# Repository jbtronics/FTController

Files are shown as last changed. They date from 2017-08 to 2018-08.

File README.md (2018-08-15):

# FTController

Der FTController ist eine Motorsteuerung hauptsächlich entwickelt für Fischertechnik. Mittels zweier Joysticks lassen sich 4 analoge Motorausgänge, plus ein Digitalausgang steuern.

## Funktionen
* 4 (bipolare) Analoge Motorausgänge, verschiedene Übertragungsfunktionen auswählbar (digital, linear, quadratisch, logarithmisch, etc.)
* 1 (unipolarer) Digitaler Leistungsausgang (schaltbar über rechten Joysticktaster)
* 1 Impulszähleingang, für Frequenz oder Umdrehungszahlmessung (mit einstellbarem Multiplikator und Teilungsverhältnis)
* Eingangsspannung und Ausgangsstrommessung
* Virtuelle Einrastfunktion: Wird während der Bedienung der Joysticks der linke Joystick doppelt gedrückt, so wird der aktuelle Wert eingefroren (d.h. der Motorwert wird beibehalten auch wenn der Stick losgelassen wird)
* Ansteuermöglichkeit für Raupenketten (Vor/Rück, Links/Rechts-Bewegung an den Joysticks wird auf Raupenkettenantrieb umgesetzt)
* Möglichkeit zur Funkübertragung vorgesehen, d.h. zukünftig auch drahtlose Steuerung möglich.

## Technische Daten
* Eingangsspannungsbereich: 7 - 15 V; Empfohlen: 8 - 10V
* Strombelastbarkeit (Summe aller Ausgänge): max 1,5A
* Strombelastbarkeit *OUT*-Ausgang: max. 500mA
* ATMega328 als Steuerung, d.h. Firmware-Updates via ISP möglich
* Software Arduino kompatibel

## Lizenzen
Für Details siehe `LICENSE.md` in den entsprechenden Verzeichnissen.
* Software: Die Software steht unter der General Public License 3.0
* Hardware: Die Design-Files für die Hardware stehen unter "Creative Commons Attribution-NonCommercial 4.0 International (CC BY-NC 4.0)"

## Benötigte Bauteile
[Hier](https://hackaday.io/project/20349/components) kann eine Liste benötigter Bauteile gefunden werden. Keine Garantie auf Vollständigkeit, sicherer ist der Schaltplan oder die interaktive Bauteileliste die unter `hardware/bom` gefunden werden kann.

## Galerie:
### PCB:
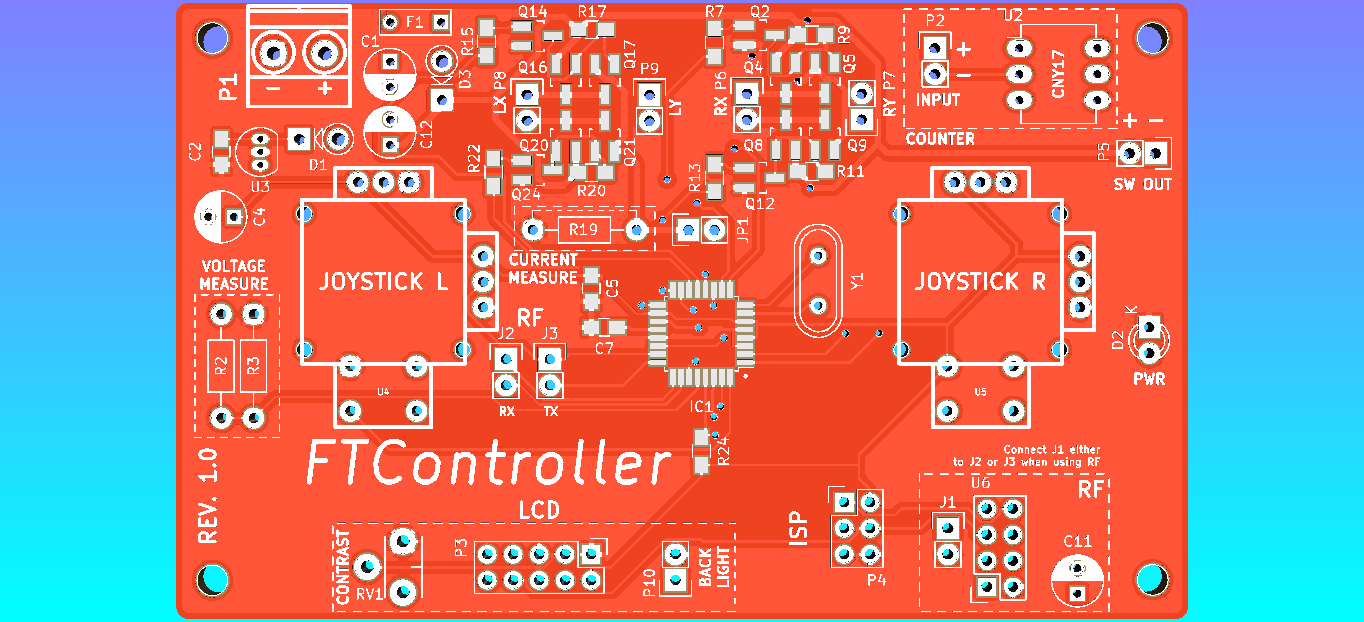
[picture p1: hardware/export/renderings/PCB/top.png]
PCB1

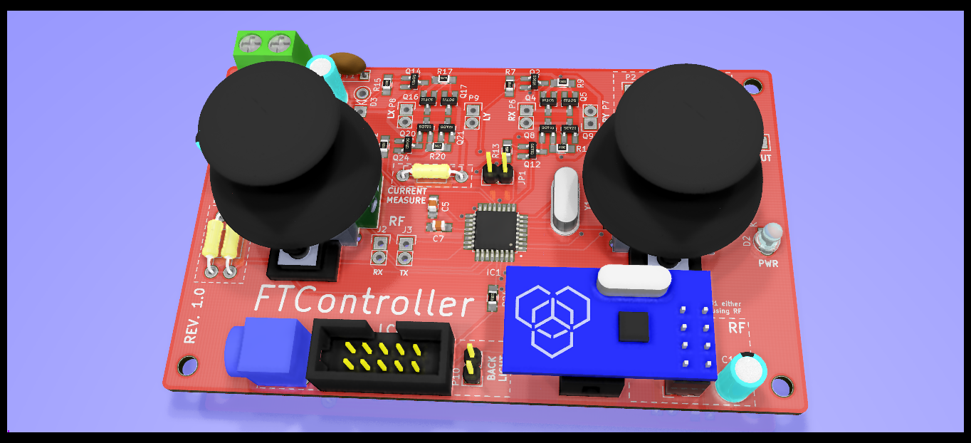
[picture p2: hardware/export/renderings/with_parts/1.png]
PCB2


### Fertiges Gerät:
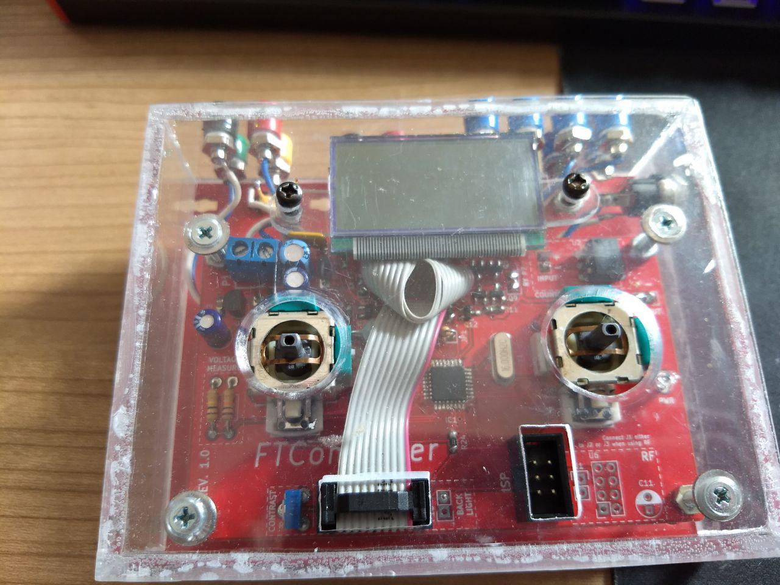
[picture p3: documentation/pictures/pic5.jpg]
finished1

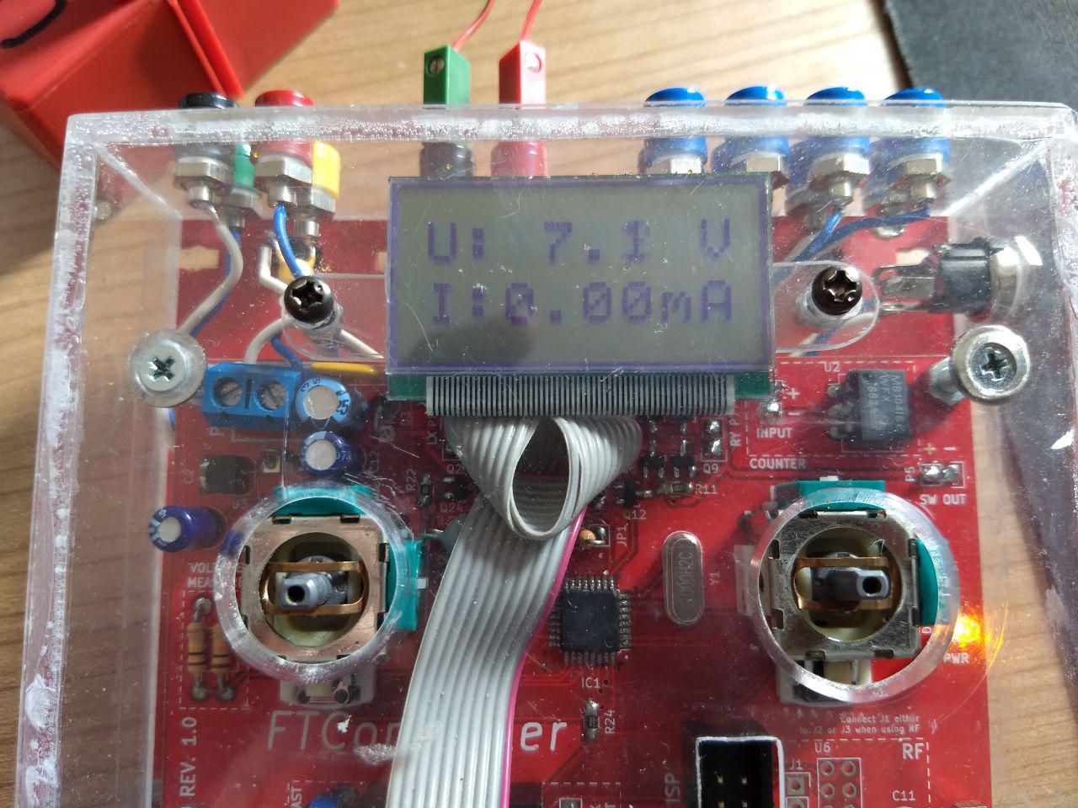
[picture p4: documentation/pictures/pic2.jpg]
finished2


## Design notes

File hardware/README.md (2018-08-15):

# FTController - Hardware

In this folder you can find the KiCAD project for the FTController PCB.
Open FTController with KiCAD 5, and enjoy...

## Some interesting folders

* `bom`: An interactive HTML page which shows, which parts are needed for the PCB and where they are placed. (Generated using [this](https://github.com/openscopeproject/InteractiveHtmlBom))
* `export`: Here you can find some renderings of the PCB
* `gerber`: Here you can find the gerber files for the PCB.

## Changelog

* *Version 1.0*: Initial Version
* *Version 1.1*: Fixed the problem that the Basis pin were used on the CNY17 optocoupler instead of the collector.

## License
The hardware design files are licensed under "Creative Commons Attribution-NonCommercial 4.0 International (CC BY-NC 4.0)". See [here](https://creativecommons.org/licenses/by-nc/4.0/) for more infos.

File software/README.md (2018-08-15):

# FTController - Software
In this folder you can find the software for the FTController:
It can be opened with the Arduino IDE or Visual Studio with the VisualMicro Extension.

Use "Arduino Pro Or Pro Mini" Board with ATMega328 CPU and 16MHz as target and it should work fine with the FTController PCB. The FTController does not have an Serial port, so you will need an ISP Programmer (like the USBasp) to flash the Sketch.

Under the `bin/` folder you can find a compiled Hex file for the FTController, which can be flashed directly onto the FTController board.

### Fuses
TODO

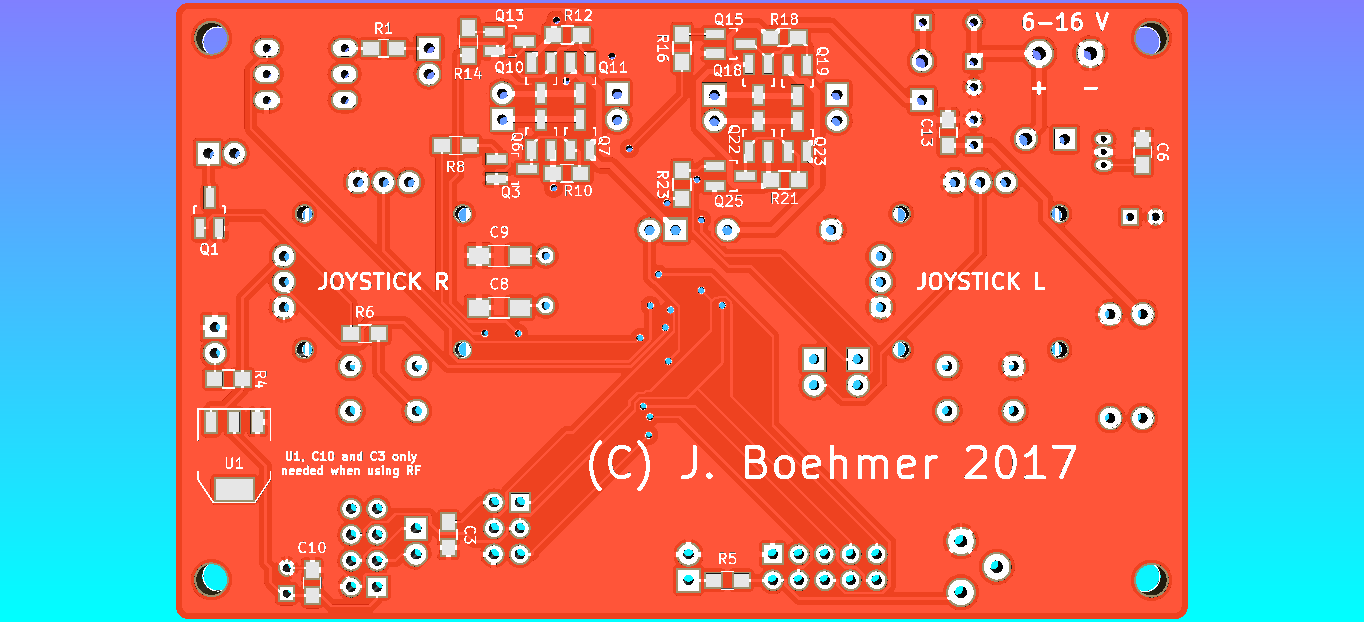
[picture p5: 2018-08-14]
hardware/export/renderings/PCB/bottom.png

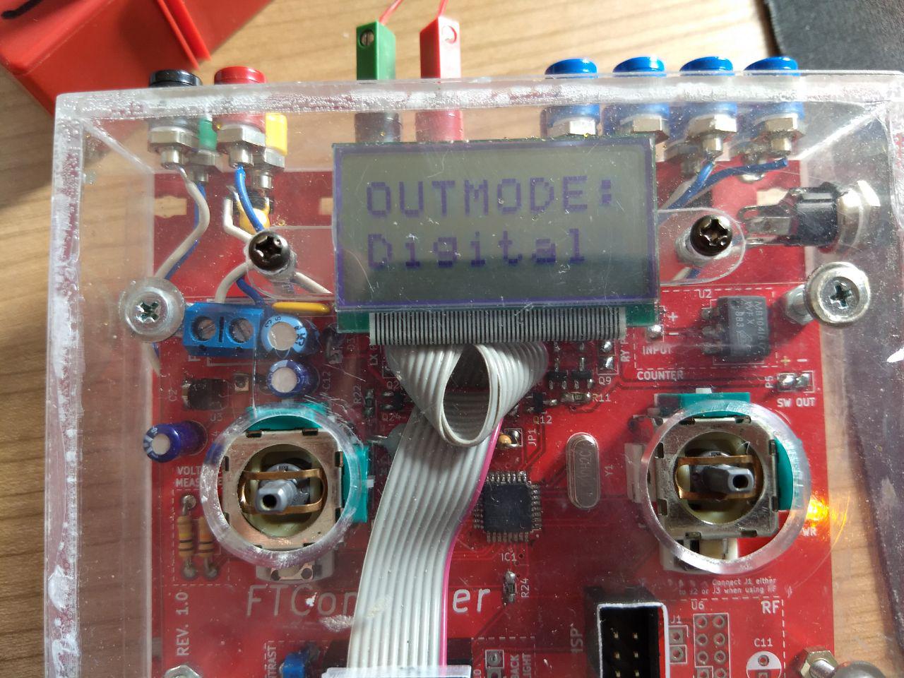
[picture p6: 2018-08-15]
documentation/pictures/pic1.jpg

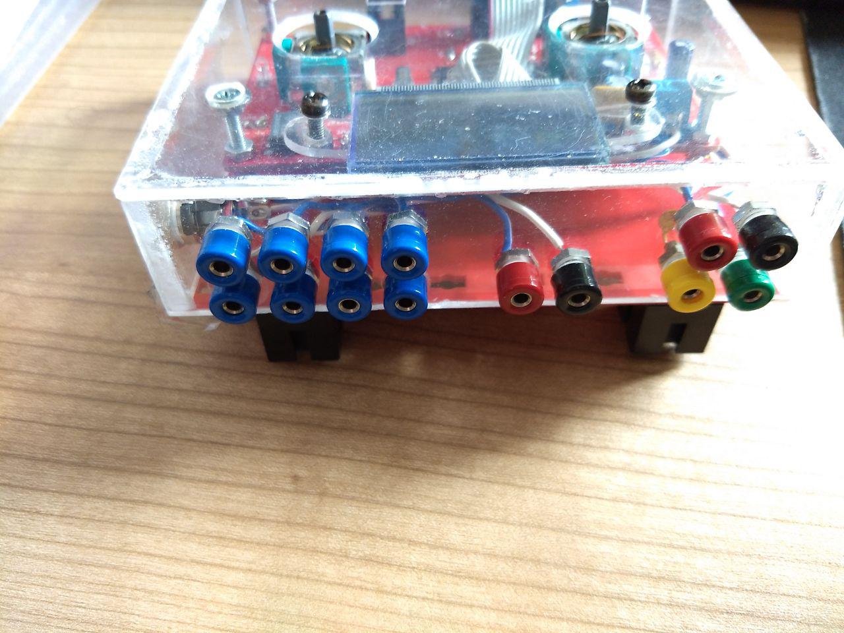
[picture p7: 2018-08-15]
documentation/pictures/pic4.jpg

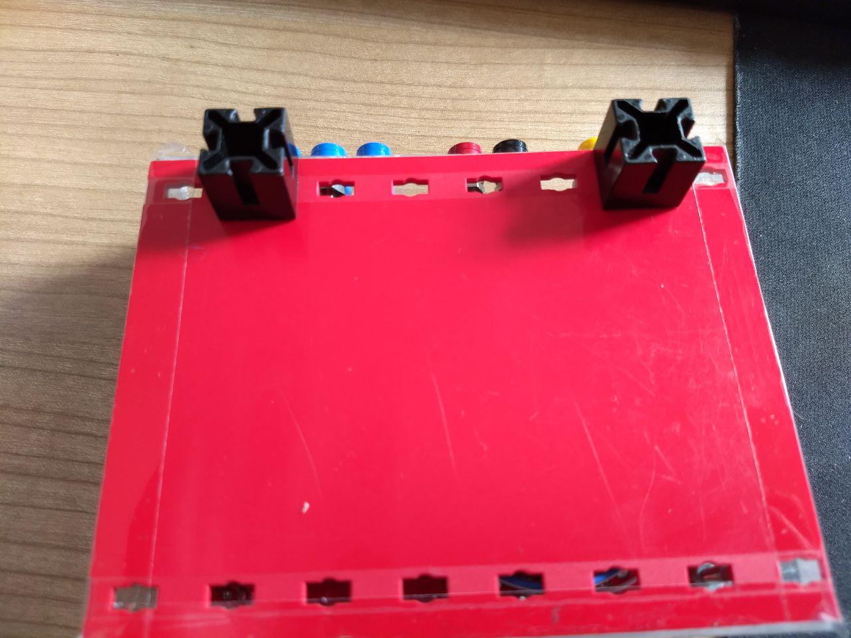
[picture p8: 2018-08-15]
documentation/pictures/pic3.jpg

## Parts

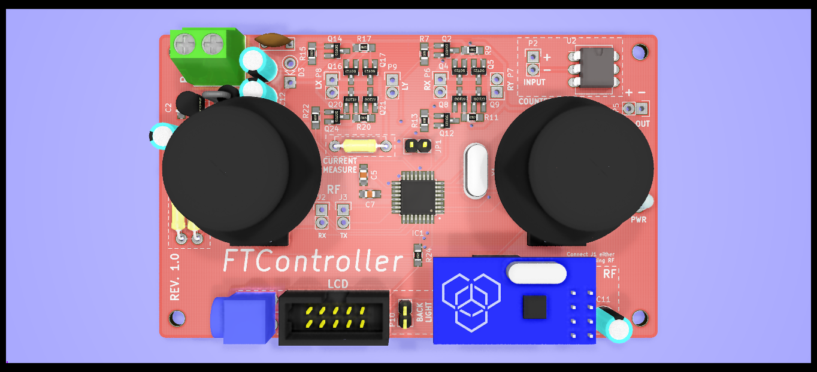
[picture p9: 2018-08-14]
hardware/export/renderings/with_parts/top.png

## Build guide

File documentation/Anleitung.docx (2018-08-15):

# FTController: Handbuch

Firmwareversion: 1.1

# Funktionen

- 4 Analoge Motorausgänge, mit verschiedenen Kennlinien
- 1 Digitaler Motorausgang
- Frequenzzähler / Umdrehungszahlmesser
- Impulszähler
- Spannungs- und Strommessung
- Unterstützung von Multiplikatoren und Teilern für die Zähloperationen
- Notausfunktion.

# Anschlüsse

Der FTController hat verschiede Anschlüsse, deren Aufgaben durch die verwendeten Buchsenfarben unterschieden werden können:

- 1x Stromversorgung, bezeichnet als PWR (rot: +, schwarz: -)
- 4x analoge Ausgänge, steuerbar per Joysticks, bezeichnet als LX, LY, RX und RY (blau)
- 1x digitaler Ausgang, schaltbar mit Drücken des rechten Joysticks, bezeichnet als OUT (rot: +, gelb: -)
- 1x galvanisch getrennter Eingang, bezeichnet als IN (grün: +, schwarz: -). Da der Eingang galvanisch isoliert ist, müssen immer beide Pole des Eingangs verwendet werden. Wenn eine Spannung zwischen den beiden Polen des Eingangs anliegt, so gilt dies als HIGH. Hinweis: Der Eingang detektiert nur steigende Flanken.

# Technische Daten

- Eingangsspannungsbereich: 7V – 15V; Empfohlen: 8 – 10V
- Strombelastbarkeit (Summe aller Ausgänge): max. 1,5A
- Strombelastbarkeit OUT-Ausgang: max. 500Ma

# Inbetriebnahme

1. Legen Sie eine Spannungsquelle (z.B. eine Batterie, Akku, oder Netzteil), ein Stromkabel und den FTController bereit.
2. Verbinden sie den Pluspol der Spannungsquelle (siehe Schritt 1) mit dem Pluspol (rot) des FTControllers unter zu Hilfenahme des Stromkabels, verfahren Sie so ebenfalls mit dem Minuspol der Batterie bzw. des FTControllers.
3. Sollten Sie eine Spannungsquelle verwenden, deren Spannungsausgabe abschaltbar ist, dann versichern Sie sich jetzt, dass die Spannung aktiviert ist. Falls dies nicht der Fall sein, aktivieren Sie die Ausgabe ihre Spannungsquelle. Sollten Sie hierbei Hilfe benötigen, konsultieren Sie bitte das Handbuch ihrer Spannungsquelle.
4. Wenn die Spannung am FTController, sollte die gelbe PWR LED aufleuchten und der FTController sollte starten.
5. Warten Sie die letzte Ausgabe der Startup Sequenz verschwunden ist. Sie können den FTController nun verwenden.

# Bedienung

- Im Steuermodus (nach Start automatisch aktiv), lassen sich mit Hilfe der Joysticks die blauen Analogausgänge steuern: Der linke Joystick steuert mit rechts/links Bewegung den LX Ausgang, mit einer oben/unten Bewegung den LY Ausgang. Der rechte Joystick steuert mit rechts/links den RX Ausgang und mit oben/unten den RY Ausgang
- Mit Druck auf den rechten Joystick, wird auf dem Digitalausgang OUT eine Spannung angelegt.
- Mit einem einfachen Klick des linken Joysticks wird das Menü geöffnet, dieses kann mit einem weiteren Klick auf den linken Joysticks wieder geschlossen werden.
- Mit einem Doppelklick auf den linken Joystick, werden die aktuellen Joystickpositionen eingefroren, d.h. alle Analogausgänge behalten den Wert bei, den sie hatten als die Ausgabe eingefroren wurde, auch wenn die Joysticks losgelassen werden. Das Display des Controllers sollte nun die Ausgabe FREEZED zeigen. Mit einem weiteren Doppelklick auf den linken Joystick wird in den normalen Steuermodus zurückgekehrt.

# Menü:

Das Menü hat drei verschiedene Bereiche zwischen denen mit dem linken Joystick oben/unten gewechselt werden kann: OUTMODE, DISPLAY und CONFIG MENU. Jeder dieser Bereiche hat verschiede Einträge, zwischen denen mit linker Joystick links/rechts gewechselt werden kann. Mit Klick auf den linken Joystick werden die getätigten Einstellungen gespeichert und das Menü geschlossen.

## OUTMODE Menü:

Mit OUTMODE lässt sich festlegen, wie genau die Joystickposition auf die Ausgänge umgesetzt werden soll:

- OUTMODE: None : Wenn dieser Modus gewählt ist, sind die Motorausgänge immer inaktiv, unabhängig von den realen Positionen der Joysticks. Beachten Sie, dass der Digitalausgang, aktivierbar durch Druck auf den rechten Joystick, davon unberührt bleibt.
- OUTMODE: Digital : In diesem Modus sind die Motorausgänge inaktiv, bis ein bestimmter Schwellenwert mit den Joysticks überschritten wird, danach sind die Motorausgänge voll durchgeschaltet.
- OUTMODE: Linear : In diesem Modus wird die Joystickposition linear auf die Ausgänge übertragen, d.h. die Kraft eines angeschlossenen Motors korrespondiert mit der Auslenkung der Joysticks. Beachten Sie, dass dies der Modus mit der höchsten Auflösung (255 Stufen) ist, alle nachfolgenden Analogmodi erlauben nur 26 Stufen.
- OUTMODE: Exp : In diesem Modus wird die Joystickposition mittels einer exponentiellen Kennlinie ausgegeben. Dies erlaubt eine sehr empfindliche Steuerung im niedrigen Bereich der Ausgabewerte.
- OUTMODE: Square : In diesem Modus wird die Joystickposition mittels einer quadratischen Kennlinie ausgegeben. Dies erlaubt eine empfindliche Steuerung im niedrigen Bereich der Ausgabewerte. Dieser Modus ist weniger empfindlich als Exp.
- OUTMODE: Log : In diesem Modus wird die Joystickposition mittels einer logarithmischen Kennlinie ausgegeben. Dies erlaubt eine empfindliche Steuerung im oberen Bereich der Ausgabewerte.
- OUTMODE: Sqrt : In diesem Modus wird die Joystickposition mittels einer Wurzel Kennlinie ausgegeben. Dies erlaubt eine empfindliche Steuerung im oberen Bereich der Ausgabewerte. Dieser Modus ist weniger empfindlich als Log.
- OUTMODE: Tank 2: Dieser Modus erlaubt die analoge Steuerung eines raupenkettengetriebenen Fahrzeuges. Dabei werden die Werte des linken Joysticks mit Hilfe eines Kreuzmischers auf die LX und LY Ausgänge umgesetzt. Das führt dazu das beim Fahren einer Kurve beide Motoren gegensinnig angesteuert werden.

Nur der linke Joystick hat diesen Modus, der rechte Joystick erlaubt die normale lineare Steuerung von Verbrauchern.

- OUTMODE: Tank 1: Dieser Modus erlaubt ähnlich wie Tank 2, die Steuerung eines kettengetriebenen Fahrzeuges, mit dem Unterschied, dass für eine Rechts/Links-Kurve nur ein Motor angesteuert wird.

## DISPLAY Menü:

Mit DISPLAY lässt sich festlegen, was für eine Anzeige während des Steuermodus erfolgen soll, so kann z.B. die aktuelle Spannung oder der Stromfluss angezeigt werden:

- DISPLAY: In Vals. : In diesem Modus werden die gemessenen Joystickpositionen ausgegeben. Diese liegen im Bereich zwischen -512 und 512, wobei ein Wert nahe 0 den Ruhezustand angibt.
- DISPLAY: Voltages. : In diesem Modus werden die Spannungen des FTControllers gemessen und ausgegeben. Die IN: Zeile gibt die Eingangsspannung an, während die 5V: Zeile die Spannung des Prozessors angibt (sieh sollte immer um ca. 5V liegen).
- DISPLAY: Power : In diesem Modus wird die Eingangsspannung in der Zeile U: dargestellt, während der Strom, der durch die Ausgänge fließt in der Zeile I: dargestellt wird. Beachten Sie, dass der Strom einige Sekunden zur Aktualisierung benötigt. Weiterhin fließen in die Strommessung nur die Ströme der Analogausgänge und nicht der Strom des Digitalausgang ein.
- DISPLAY: Out Vals. : In diesem Modus werden die Stärke der Ausgaben für jeden Analogausgang dargestellt. Diese reichen von -255 bis 255, wobei 0 keine Ausgabe bedeutet. Beachten sie, dass dieser Modus nicht bei den OUTMODEs LINEAR oder DIGITAL funktioniert.
- DISPLAY: RPM : In diesem Modus wird die Frequenz bzw. daraus abgeleitet, die Umdrehungszahl die am Eingang anliegt gemessen. Die erste Zeile der Ausgabe, gibt die Einheit an mit der die Ausgabe erfolgt, während die zweite Zeile den gemessenen Wert zeigt. Sollte die Input Entprellung (siehe I.DEBNC. im Config menu) aktiviert sein, so wird dies mit einem D in der ersten Zeile kenntlich gemacht. Ein möglicherweiser aktiver Multiplikator (siehe C.MULTI und C.DIVIDE) wird mit x gekennzeichnet. Die Einheit mit der die Ausgabe erfolgt kann mit der C.UNIT Einstellung im Config menu verändert werden. Die maximale Frequenz, die gemessen werden kann, beträgt ca. 100kHz.
- DISPLAY: COUNTER : In diesem Modus wird für jede aufsteigende Flanke am Eingang der Zähler inkrementiert. Dabei werden die Multiplikatoren und Divisor Einstellungen berücksichtigt. Um den Zähler auf 0 zurücksetzen, muss man einen Doppelklick auf den linken Joystick durchführen.
- DISPLAY: TEMP : Dieser Modus zeigt die ungefähre Temperatur des Prozessors in Grad Celsius an. Da der Temperatursensor nicht kalibriert ist, sollte nur die Veränderungen des Temperaturwertes zur Kontrolle herangezogen werden, nicht der absolute Wert.

## CONFIG MENU Menü

In diesem Menü lassen sich verschieden Einstellungen treffen, die vor allem den COUNTER/RPM Modus betreffen. Mit dem linken Joystick links/rechts lässt sich die Einstellung auswählen, die bearbeitet werden soll und mit dem rechten Stick lässt sich der Wert verändern. Soll eine Zahl eingegeben werden, so verändert rechter Stick rechts/links den Wert in 1er-Schritten, während oben/unten den Wert in 10er-Schritten verändert:

- EM. HALT: Nothalt-Funktion: Wenn diese Funktion aktiviert ist, dann werden, sobald eine postive Flanke am Eingang erkannt wird, alle Ausgänge deaktiviert. Auf dem Display sollte dann die Ausgabe Em.Halt! PressBTN erscheinen. Wenn man wieder in den normalen Modus zurückkehren will, so muss man den linken Joystick drücken.
- C. UNIT: Mit dieser Einstellung lässt sich die Einheit einstellen, mit der im RPM Modus die Ausgabe erfolgen soll. Mögliche Werte: RPM oder Hz.
- I. DEBNC.: Entprellung. Wenn diese Einstellung aktiv ist, dann wird der Eingang entprellt, d.h. die Anzahl der maximalen Flanken pro Sekunde wird reduziert. Diese Einstellung sollte aktiviert werden, wenn bei einem einzigen Schalterklick, mehrere Klicks gezählt werden.
- C. MULTI: Dieser Wert stellt den Multiplikator ein, mit dem die Zahl der Inputsignale multipliziert wird. Steht C.MULTI z.B. auf 2, so zählt jedes Eingangssignal doppelt.
- C. DIVIDE: Dieser Wert stellt den Multiplikator ein, mit dem die Zahl der Inputsignale dividiert wird. Steht C.DIVIDE z.B. auf 2, so muss zwei Mal ein Signal auftreten, damit der Wert hochgezählt wird.

# Weitere Hinweise:

- Erscheint beim Start die Meldung RELEASE STICKS!, so müssen die Sticks losgelassen werden, um fortzufahren. Dies verhindert, dass ein Motor sofort nach dem Start aktiviert wird.
- Erscheint die Meldung Ov.Curr! PressBTN, so wurde ein zu hoher Strom gemessen. Dies kann eventuell auf einen Kurzschluss hinweisen. Möchte man fortfahren, so muss der linke Joystick gedrückt werden.
- Startet sich der FTController ohne Unterbrechung der Stromversorgung selbständig neu, so weist dies auf einen Kurzschluss hin. Beheben Sie diesen bevor Sie fortfahren.

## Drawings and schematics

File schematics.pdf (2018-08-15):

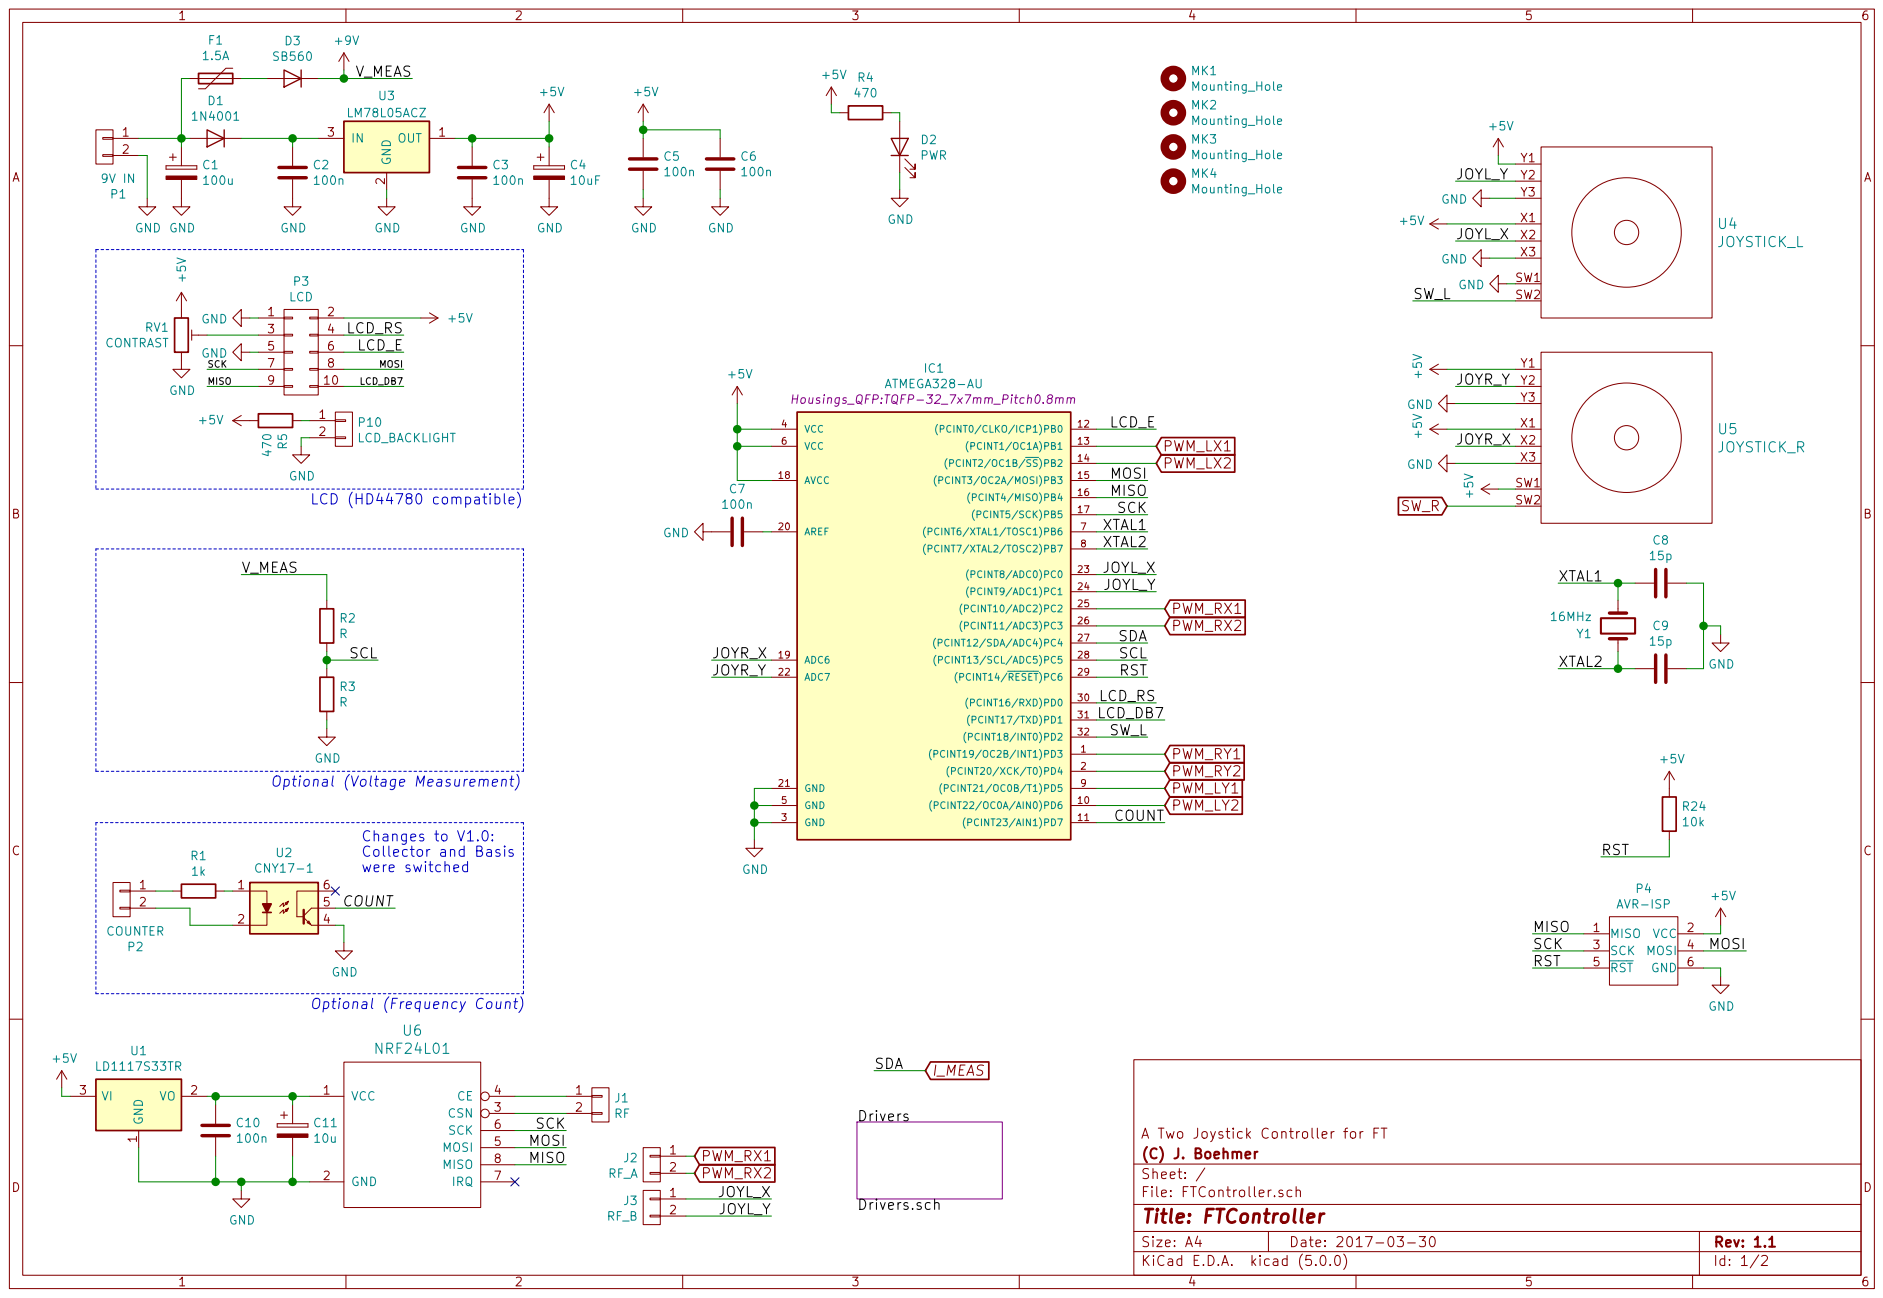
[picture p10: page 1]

Collector and Basis were switched

A Two Joystick Controller for FT
Id: 1/2 Title: FTController File: FTController.sch Sheet: / (C) J. Boehmer

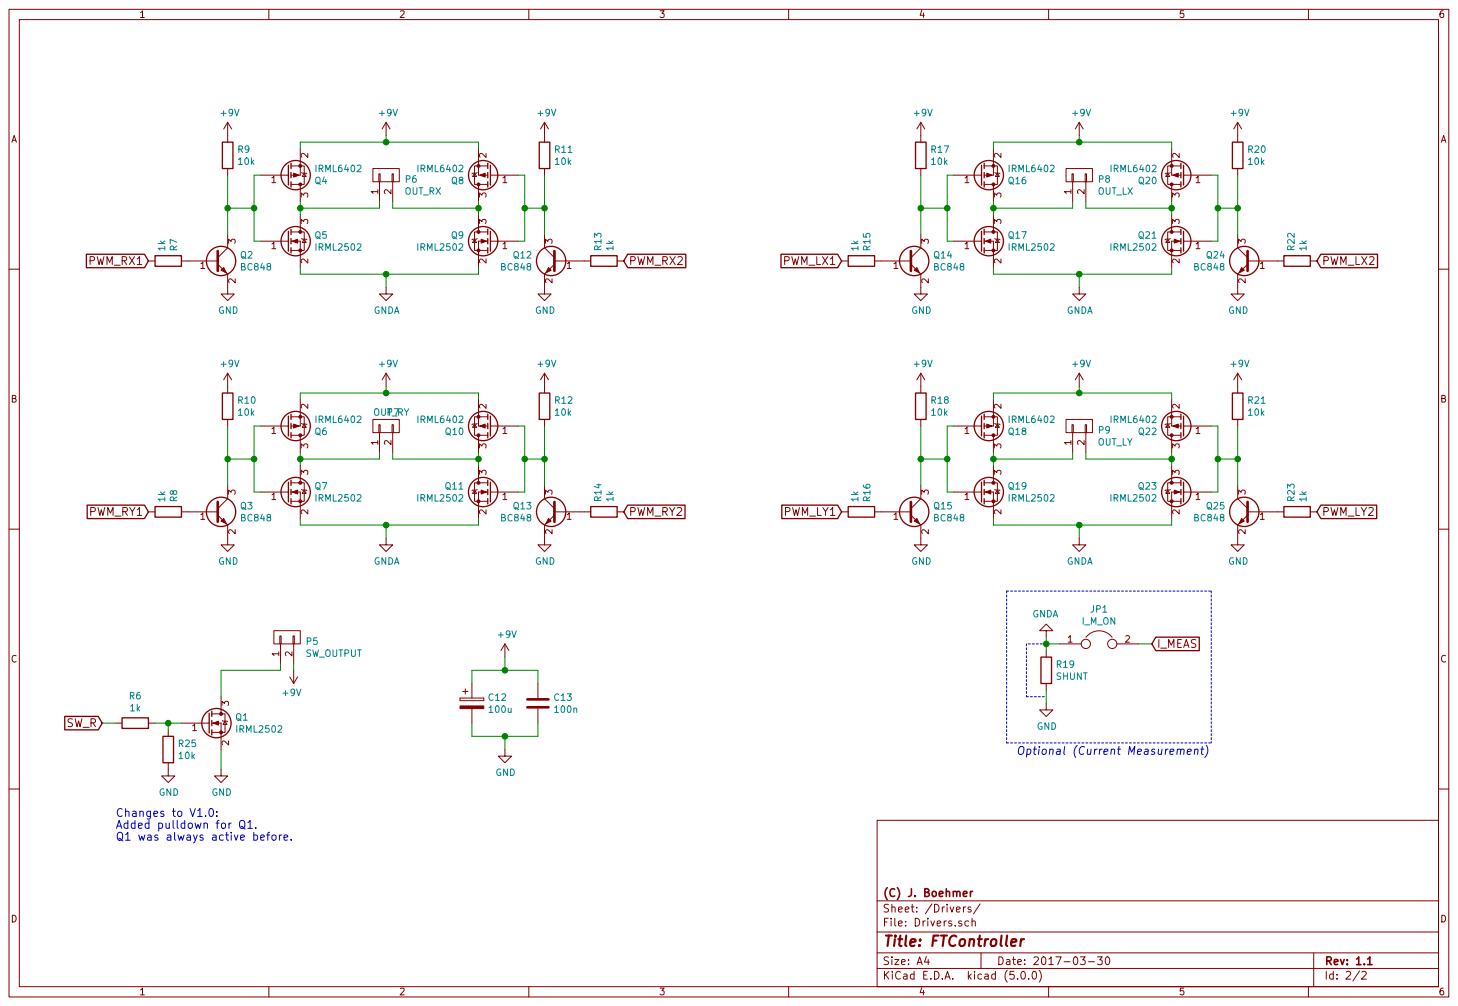
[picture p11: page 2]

Added pulldown for Q1.
Q1 was always active before.

Id: 2/2 Title: FTController File: Drivers.sch Sheet: /Drivers/ (C) J. Boehmer

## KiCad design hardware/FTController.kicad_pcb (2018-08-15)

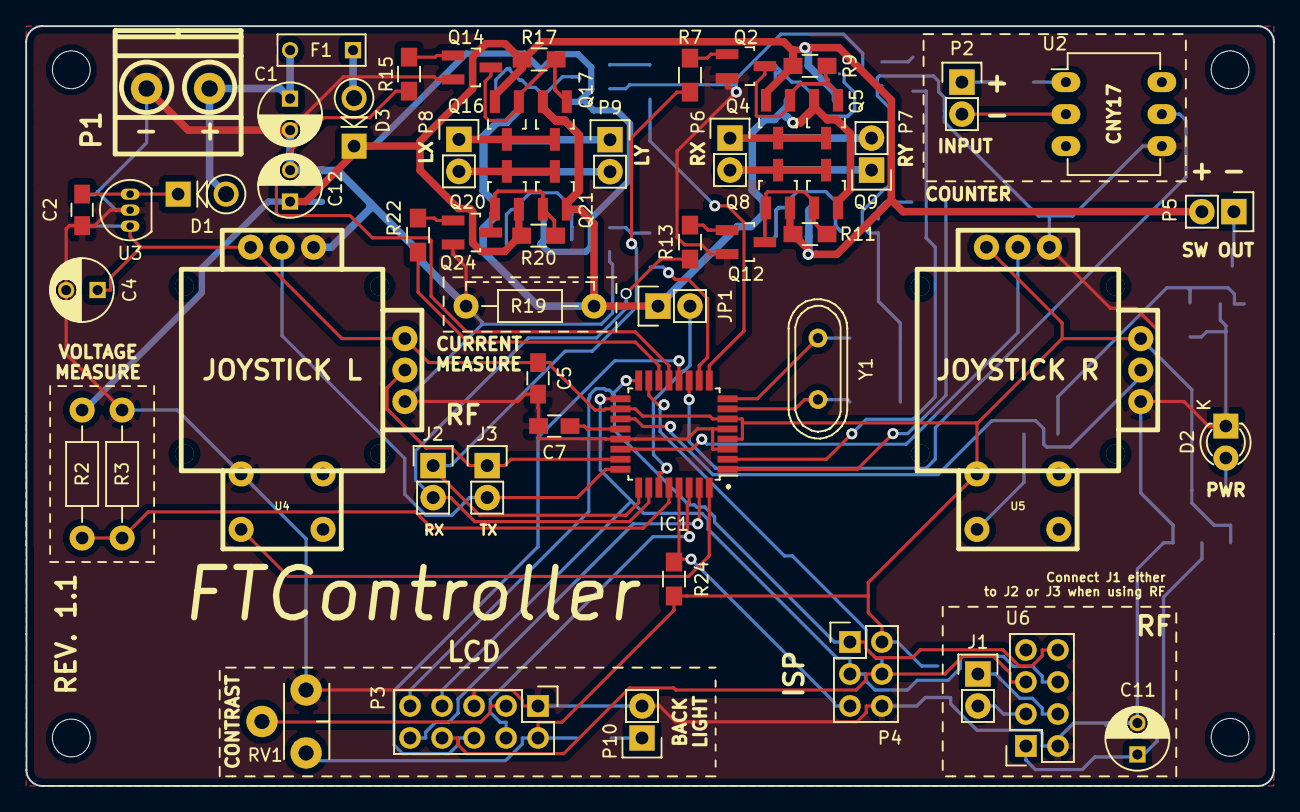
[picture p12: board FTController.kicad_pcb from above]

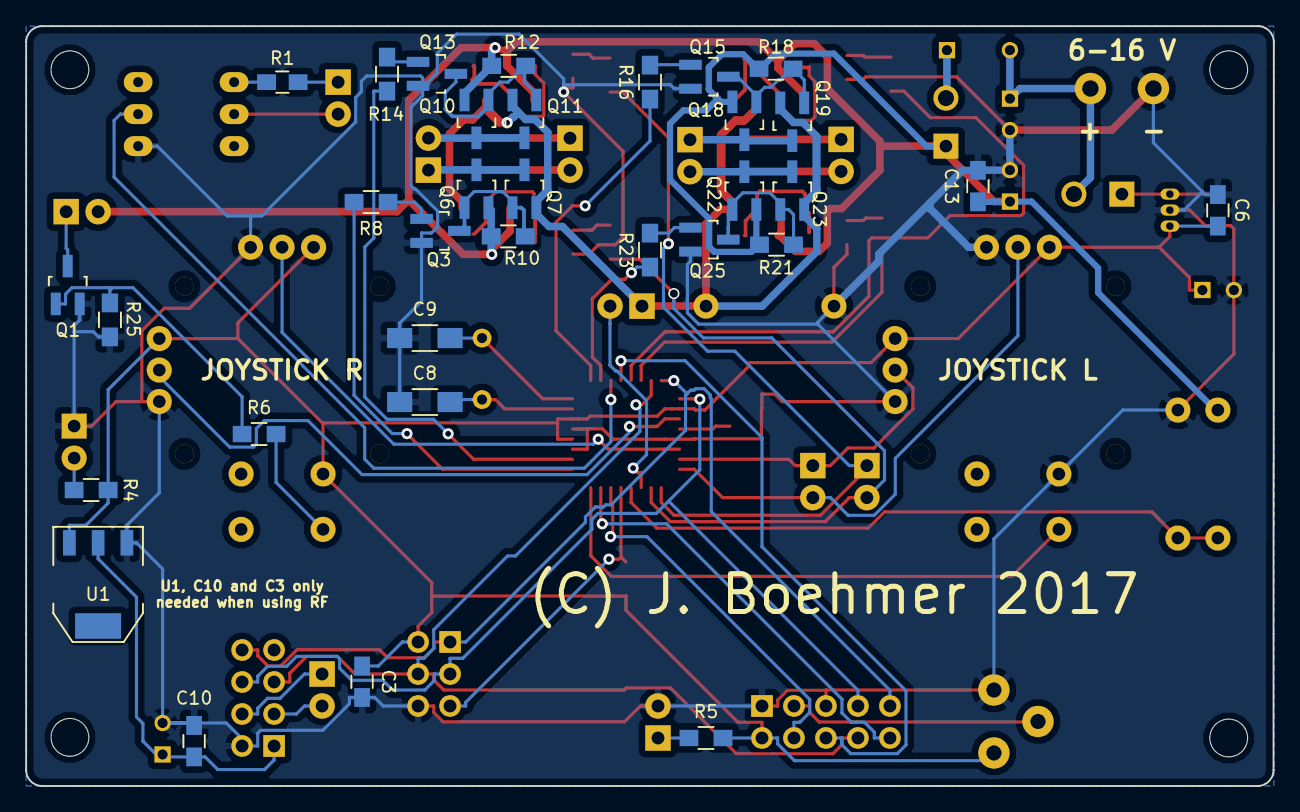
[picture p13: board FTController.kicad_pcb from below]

Board: 2 copper layers, 99.1 x 60.3 mm, 94 parts (33 on the bottom side), 69 nets.

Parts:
C1, C12: 100u; C_Radial_D5_L11_P2.5
C2, C3, C5, C6, C7, C10, C13: 100n; C_0805_HandSoldering
C4: 10uF; C_Radial_D5_L11_P2.5
C8, C9: 15p; C_1206_HandSoldering
C11: 10u; C_Radial_D5_L11_P2.5
D1: 1N4001; Diode_DO-41_SOD81_Vertical_KathodeUp
D2: PWR; LED-3MM
D3: SB560; Diode_DO-41_SOD81_Vertical_KathodeUp
F1: 1.5A; C_Rect_L7_W2.5_P5
IC1: ATMEGA328-AU; TQFP-32_7x7mm_Pitch0.8mm
J1: RF; Pin_Header_Straight_1x02
J2: RF_A; Pin_Header_Straight_1x02
J3: RF_B; Pin_Header_Straight_1x02
JP1: I_M_ON; Pin_Header_Straight_1x02
MK1, MK2, MK3, MK4: Mounting_Hole; MountingHole_3mm
P1: 9V IN; mkds_1,5-2
P2: COUNTER; Pin_Header_Straight_1x02
P3: LCD; Pin_Header_Straight_2x05
P4: AVR-ISP; Pin_Header_Straight_2x03
P5: SW_OUTPUT; Pin_Header_Straight_1x02
P6: OUT_RX; Pin_Header_Straight_1x02
P7: OUT_RY; Pin_Header_Straight_1x02
P8: OUT_LX; Pin_Header_Straight_1x02
P9: OUT_LY; Pin_Header_Straight_1x02
P10: LCD_BACKLIGHT; Pin_Header_Straight_1x02
Q1, Q5, Q7, Q9, Q11, Q17, Q19, Q21, Q23: IRML2502; SOT-23_Handsoldering
Q2, Q3, Q12, Q13, Q14, Q15, Q24, Q25: BC848; SOT-23_Handsoldering
Q4, Q6, Q8, Q10, Q16, Q18, Q20, Q22: IRML6402; SOT-23_Handsoldering
R1: 1k; C_0805_HandSoldering
R2, R3: R; Resistor_Horizontal_RM10mm
R4, R5: 470; R_0805_HandSoldering
R6, R7, R8, R13, R14, R15, R16, R22, R23: 1k; R_0805_HandSoldering
R9, R10, R11, R12, R17, R18, R20, R21, R24, R25: 10k; R_0805_HandSoldering
R19: SHUNT; Resistor_Horizontal_RM10mm
RV1: CONTRAST; Potentiometer_VishaySpectrol-Econtrim-Type36X
U1: LD1117S33TR; SOT-223
U2: CNY17-1; DIP-6_W7.62mm_LongPads
U3: LM78L05ACZ; TO-92_Inline_Narrow_Oval
U4: JOYSTICK_L; Joystick_Button
U5: JOYSTICK_R; Joystick_Button
U6: NRF24L01; Socket_Strip_Straight_2x04
Y1: 16MHz; Crystal_HC49-U_Vertical

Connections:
+5V: C3.1, C4.1, C5.1, C6.1, IC1.4, IC1.6, IC1.18, P3.2, P4.2, R4.2, R5.2, R24.1, RV1.1, U1.3, U3.1, U4.X1, U4.Y1, U5.SW1, U5.X1, U5.Y1
+9V: C12.1, C13.1, D3.1, P5.2, Q4.2, Q6.2, Q8.2, Q10.2, Q16.2, Q18.2, Q20.2, Q22.2, R2.1, R9.1, R10.1, R11.1, R12.1, R17.1, R18.1, R20.1, R21.1
/COUNT: IC1.11, U2.5
/JOYL_X: IC1.23, J3.1, U4.X2
/JOYL_Y: IC1.24, J3.2, U4.Y2
/JOYR_X: IC1.19, U5.X2
/JOYR_Y: IC1.22, U5.Y2
/LCD_DB7: IC1.31, P3.10
/LCD_E: IC1.12, P3.6
/LCD_RS: IC1.30, P3.4
/MISO: IC1.16, P3.9, P4.1, U6.8
/MOSI: IC1.15, P3.8, P4.4, U6.5
/RST: IC1.29, P4.5, R24.2
/SCK: IC1.17, P3.7, P4.3, U6.6
/SCL: IC1.28, R2.2, R3.1
/SW_L: IC1.32, U4.SW2
/XTAL1: C8.2, IC1.7, Y1.2
/XTAL2: C9.2, IC1.8, Y1.1
GND: C1.2, C2.2, C3.2, C4.2, C5.2, C6.2, C7.2, C8.1, C9.1, C10.2, C11.2, C12.2, C13.2, D2.1, IC1.3, IC1.5, IC1.21, P1.2, P3.1, P3.5, P4.6, P10.2, Q1.2, Q2.2, Q3.2, Q12.2, Q13.2, Q14.2, Q15.2, Q24.2, Q25.2, R3.2, R19.2, R25.2, RV1.3, U1.1, U2.4, U3.2, U4.SW1, U4.X3, U4.Y3, U5.X3, U5.Y3, U6.2
GNDA: JP1.1, Q5.2, Q7.2, Q9.2, Q11.2, Q17.2, Q19.2, Q21.2, Q23.2, R19.1
I_MEAS: IC1.27, JP1.2
unnamed: C1.1, D1.2, F1.2, P1.1
unnamed: C2.1, D1.1, U3.3
unnamed: C7.1, IC1.20
unnamed: C10.1, C11.1, U1.2, U6.1
unnamed: D2.2, R4.1
unnamed: D3.2, F1.1
unnamed: J1.1, U6.4
unnamed: J1.2, U6.3
unnamed: P2.1, R1.2
unnamed: P2.2, U2.2
unnamed: P3.3, RV1.2
unnamed: P5.1, Q1.3
unnamed: P6.1, Q4.3, Q5.3
unnamed: P6.2, Q8.3, Q9.3
unnamed: P7.1, Q6.3, Q7.3
unnamed: P7.2, Q10.3, Q11.3
unnamed: P8.1, Q16.3, Q17.3
unnamed: P8.2, Q20.3, Q21.3
unnamed: P9.1, Q18.3, Q19.3
unnamed: P9.2, Q22.3, Q23.3
unnamed: P10.1, R5.1
unnamed: Q1.1, R6.1, R25.1
unnamed: Q2.1, R7.1
unnamed: Q2.3, Q4.1, Q5.1, R9.2
unnamed: Q3.1, R8.1
unnamed: Q3.3, Q6.1, Q7.1, R10.2
unnamed: Q10.1, Q11.1, Q13.3, R12.2
unnamed: Q12.1, R13.1
unnamed: Q8.1, Q9.1, Q12.3, R11.2
unnamed: Q13.1, R14.1
unnamed: Q14.1, R15.1
unnamed: Q14.3, Q16.1, Q17.1, R17.2
unnamed: Q15.1, R16.1
unnamed: Q15.3, Q18.1, Q19.1, R18.2
unnamed: Q20.1, Q21.1, Q24.3, R20.2
unnamed: Q22.1, Q23.1, Q25.3, R21.2
unnamed: Q24.1, R22.1
unnamed: Q25.1, R23.1
unnamed: R1.1, U2.1
PWM_LX1: IC1.13, R15.2
PWM_LX2: IC1.14, R22.2
PWM_LY1: IC1.9, R16.2
PWM_LY2: IC1.10, R23.2
PWM_RX1: IC1.25, J2.1, R7.2
PWM_RX2: IC1.26, J2.2, R13.2
PWM_RY1: IC1.1, R8.2
PWM_RY2: IC1.2, R14.2
SW_R: R6.2, U5.SW2

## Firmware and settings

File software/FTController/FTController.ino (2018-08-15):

/*
Copyright (C) 2017  Jan Böhmer

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
You should have received a copy of the GNU General Public License
along with this program.  If not, see <https://www.gnu.org/licenses/>.
*/


#include <EEPROM.h>
#include <InputDebounce.h>
#include "helpers.h"
#include "config.h"
#include "chars.h"
#include <LiquidCrystal.h>
#include <PinChangeInt.h>
#include "menu.h"

//Global objects
LiquidCrystal lcd(LCD_RS, LCD_E, LCD_D4, LCD_D5, LCD_D6, LCD_D7);
static InputDebounce button;

uint8_t menu = MENU_HIDDEN;

uint8_t mode = MODE_DEFAULT;
uint8_t display_mode = DISPLAY_DEFAULT;
uint8_t config_mode = CONFIG_DEFAULT;
uint8_t emergency_halt;
uint8_t freeze = 0;

uint8_t failsafe = FAILSAFE_OFF;

config_struct config;

int16_t joysticks[4];
int16_t output_val[4];

void setup()
{
	
	init_all();
	analogReference(DEFAULT);
	lcd.begin(8, 2);

	config.emergency_halt = 0; //Disable emergency halt by default

	//Show Startup banner
	startup_banner();

	read_eeprom();
	//Override read modes
	//mode = MODE_DIGITAL;
	//mode = MODE_ANALOG;
	//display_mode = DISPLAY_VOLT;

	PCattachInterrupt(PIN_COUNT, pcint_handler, FALLING);

	button.registerCallbacks(button_pressedCallback, button_releasedCallback, button_pressedDurationCallback);
	button.setup(SW_L);
}

void loop()
{
	//update_volt();

	//First check for failsafe
	failsafe_check();

	//Always read joystick values
	read_joysticks();
	
	if (failsafe == FAILSAFE_OFF)
	{
		if (menu == MENU_HIDDEN) //Only execute Modes if Menu is hidden
		{
			switch (mode)
			{
			case MODE_DIGITAL:
				mode_digital();
				break;
			case MODE_ANALOG:
				mode_analog();
				break;
			case MODE_EXP:
				mode_exp();
				break;
			case MODE_SQUARE:
				mode_square();
				break;
			case MODE_LN:
				mode_log();
				break;
			case MODE_SQRT:
				mode_sqrt();
				break;
			default:
				break;
			}
		}

		update_display();
	}
	button.process(millis());

	//delay(100);
}


/*********************************************
* DISPLAY
**********************************************/
void update_display()
{
	static long lasttime = millis();
	if (millis() - lasttime > 100) //Update every 100ms
	{
		lcd.clear();
		if (menu != MENU_HIDDEN)
		{
			lasttime = millis();
			show_menu();
			return;
		}

		if (freeze == 1)
		{
			lasttime = millis();
			lcd.print("FREEZED");
			return;
		}
		switch (display_mode)
		{
		case DISPLAY_INPUT:
			display_input();
			break;
		case DISPLAY_VOLT:
			display_volt();
			break;
		case DISPLAY_POWER:
			display_power();
			break;
		case DISPLAY_OUT:
			display_out();
			break;
		case DISPLAY_RPM:
			display_rpm();
			break;
		case DISPLAY_COUNT:
			display_counter();
			break;
		case DISPLAY_TEMP:
			display_temp();
			break;
		}

		lasttime = millis();
	}
}

inline void display_input()
{
	//lcd.clear();
	lcd.setCursor(0, 0);
	lcd.print(joysticks[JOYSTICK_LX]);
	lcd.setCursor(4, 0);
	lcd.print(joysticks[JOYSTICK_LY]);
	lcd.setCursor(0, 1);
	lcd.print(joysticks[JOYSTICK_RX]);
	lcd.setCursor(4, 1);
	lcd.print(joysticks[JOYSTICK_RY]);
}

void display_volt()
{
	//Input Voltage
	lcd.setCursor(0, 0);
	lcd.print(F("IN:"));
	uint16_t val = read_input_volt();
	if (val < 10000) //Insert space if only one digit
		lcd.print(" ");
	lcd.print(val / 1000.0, 1);
	lcd.setCursor(7, 0);
	lcd.print(F("V"));

	//5V Voltage
	lcd.setCursor(0, 1);
	lcd.print(F("5V:"));
	val = read_MCU_volt();
	if (val < 10000) //Insert space if only one digit
		lcd.print(" ");
	lcd.print(val / 1000.0, 1);
	lcd.setCursor(7, 1);
	lcd.print(F("V"));
}

void display_power()
{
	//Input Voltage
	lcd.setCursor(0, 0);
	lcd.print(F("U:"));
	uint16_t val = read_input_volt();
	if (val < 10000) //Insert space if only one digit
		lcd.print(" ");
	lcd.print(val / 1000.0, 2);
	lcd.setCursor(7, 0);
	lcd.print(F("V"));

	//Output Current
	lcd.setCursor(0, 1);
	lcd.print(F("I:"));
	val = read_output_current();
	//if (val < 10000) //Insert space if only one digit
		//lcd.print(" ");
	lcd.print(val / 1000.0 , 2);
	lcd.setCursor(6, 1);
	lcd.print(F("mA"));
}

void display_out()
{
	lcd.print(output_val[JOYSTICK_LX]);
	lcd.setCursor(4, 0);
	lcd.print(output_val[JOYSTICK_LY]);
	lcd.setCursor(0, 1);
	lcd.print(output_val[JOYSTICK_RX]);
	lcd.setCursor(4, 1);
	lcd.print(output_val[JOYSTICK_RY]);
}

void display_temp()
{
	lcd.print("Temp.");
	lcd.setCursor(0, 1);
	lcd.print(GetTemp());
}

void display_rpm()
{
	static long lasttime = millis();
	static float val = 0;
	if (millis() - lasttime > 1000)
	{
		val = (counter_val() * 1000.0) / (millis() - lasttime); // * 60;
		
		if (config.counter_unit == CUNIT_RPM)
			val = val * 60;

		if (config.counter_divide)
		{
			val = val / (config.counter_divide + 1);
		}

		if (config.counter_multi)
		{
			val = val * (config.counter_multi + 1);
		}

		counter_reset();
		lasttime = millis();
	}
	if (config.counter_unit == CUNIT_HZ)
		lcd.print("Hz:");
	else if (config.counter_unit == CUNIT_RPM)
		lcd.print("RPM:");

	if (config.counter_debounce == 1)
		lcd.print(" D");	//Print hint that debounce is activated

	if (config.counter_divide || config.counter_multi)
		lcd.print(" x");

	lcd.setCursor(0,1);

	if (config.counter_unit == CUNIT_HZ)
		lcd.print(val);
	else if (config.counter_unit == CUNIT_RPM)
		lcd.print(val, 0);	//Cut digits after the point, we dont have that precision
}

void display_counter()
{
	lcd.print(F("Counter:"));
	lcd.setCursor(0, 1);
	lcd.print(counter_val());
}


/********************************************
* MODE HANDLING
*********************************************/

inline void mode_digital()
{
	//LX Joystick
	if (joysticks[JOYSTICK_LX] < THRESHOLD_N)
		motor_output_digtal(MOTOR_LX, MOTOR_FWD);
	else if (joysticks[JOYSTICK_LX] > THRESHOLD_P)
		motor_output_digtal(MOTOR_LX, MOTOR_REV);
	else
		motor_output_digtal(MOTOR_LX, MOTOR_HALT);

	//LY Joystick
	if (joysticks[JOYSTICK_LY] < THRESHOLD_N)
		motor_output_digtal(MOTOR_LY, MOTOR_FWD);
	else if (joysticks[JOYSTICK_LY] > THRESHOLD_P)
		motor_output_digtal(MOTOR_LY, MOTOR_REV);
	else
		motor_output_digtal(MOTOR_LY, MOTOR_HALT);

	//RX Joystick
	if (joysticks[JOYSTICK_RX] < THRESHOLD_N)
		motor_output_digtal(MOTOR_RX, MOTOR_FWD);
	else if (joysticks[JOYSTICK_RX] > THRESHOLD_P)
		motor_output_digtal(MOTOR_RX, MOTOR_REV);
	else
		motor_output_digtal(MOTOR_RX, MOTOR_HALT);

	//RY Joystick
	if (joysticks[JOYSTICK_RY] < THRESHOLD_N)
		motor_output_digtal(MOTOR_RY, MOTOR_FWD);
	else if (joysticks[JOYSTICK_RY] > THRESHOLD_P)
		motor_output_digtal(MOTOR_RY, MOTOR_REV);
	else
		motor_output_digtal(MOTOR_RY, MOTOR_HALT);

}

inline void mode_analog()
{
	motor_output_analog(MOTOR_LX, joysticks[JOYSTICK_LX]);
	motor_output_analog(MOTOR_LY, joysticks[JOYSTICK_LY]);
	motor_output_analog(MOTOR_RX, joysticks[JOYSTICK_RX]);
	motor_output_analog(MOTOR_RY, joysticks[JOYSTICK_RY]);
}

inline void mode_exp()
{
	output_val[JOYSTICK_LX] = map_joy_with_table(joysticks[JOYSTICK_LX], TABLE_EXP);
	output_val[JOYSTICK_LY] = map_joy_with_table(joysticks[JOYSTICK_LY], TABLE_EXP);
	output_val[JOYSTICK_RX] = map_joy_with_table(joysticks[JOYSTICK_RX], TABLE_EXP);
	output_val[JOYSTICK_RY] = map_joy_with_table(joysticks[JOYSTICK_RY], TABLE_EXP);

	motor_output_analog_raw(MOTOR_LX ,output_val[JOYSTICK_LX]);
	motor_output_analog_raw(MOTOR_LY, output_val[JOYSTICK_LY]);
	motor_output_analog_raw(MOTOR_RX, output_val[JOYSTICK_RX]);
	motor_output_analog_raw(MOTOR_RY, output_val[JOYSTICK_RY]);
}

inline void mode_square()
{
	output_val[JOYSTICK_LX] = map_joy_with_table(joysticks[JOYSTICK_LX], TABLE_SQUARE);
	output_val[JOYSTICK_LY] = map_joy_with_table(joysticks[JOYSTICK_LY], TABLE_SQUARE);
	output_val[JOYSTICK_RX] = map_joy_with_table(joysticks[JOYSTICK_RX], TABLE_SQUARE);
	output_val[JOYSTICK_RY] = map_joy_with_table(joysticks[JOYSTICK_RY], TABLE_SQUARE);

	motor_output_analog_raw(MOTOR_LX, output_val[JOYSTICK_LX]);
	motor_output_analog_raw(MOTOR_LY, output_val[JOYSTICK_LY]);
	motor_output_analog_raw(MOTOR_RX, output_val[JOYSTICK_RX]);
	motor_output_analog_raw(MOTOR_RY, output_val[JOYSTICK_RY]);
}

inline void mode_log()
{
	output_val[JOYSTICK_LX] = map_joy_with_table(joysticks[JOYSTICK_LX], TABLE_LOG);
	output_val[JOYSTICK_LY] = map_joy_with_table(joysticks[JOYSTICK_LY], TABLE_LOG);
	output_val[JOYSTICK_RX] = map_joy_with_table(joysticks[JOYSTICK_RX], TABLE_LOG);
	output_val[JOYSTICK_RY] = map_joy_with_table(joysticks[JOYSTICK_RY], TABLE_LOG);

	motor_output_analog_raw(MOTOR_LX, output_val[JOYSTICK_LX]);
	motor_output_analog_raw(MOTOR_LY, output_val[JOYSTICK_LY]);
	motor_output_analog_raw(MOTOR_RX, output_val[JOYSTICK_RX]);
	motor_output_analog_raw(MOTOR_RY, output_val[JOYSTICK_RY]);
}

inline void mode_sqrt()
{
	output_val[JOYSTICK_LX] = map_joy_with_table(joysticks[JOYSTICK_LX], TABLE_SQRT);
	output_val[JOYSTICK_LY] = map_joy_with_table(joysticks[JOYSTICK_LY], TABLE_SQRT);
	output_val[JOYSTICK_RX] = map_joy_with_table(joysticks[JOYSTICK_RX], TABLE_SQRT);
	output_val[JOYSTICK_RY] = map_joy_with_table(joysticks[JOYSTICK_RY], TABLE_SQRT);

	motor_output_analog_raw(MOTOR_LX, output_val[JOYSTICK_LX]);
	motor_output_analog_raw(MOTOR_LY, output_val[JOYSTICK_LY]);
	motor_output_analog_raw(MOTOR_RX, output_val[JOYSTICK_RX]);
	motor_output_analog_raw(MOTOR_RY, output_val[JOYSTICK_RY]);
}


/******************************************************
* HELPER FUNCTIONS
******************************************************/
void read_joysticks()
{
	if (freeze == 0) //Dont read the joysticks if the freeze mode is activated
	{
		//Calculate 
		joysticks[JOYSTICK_LX] = analogRead(JOYL_X) - MID_LX;
		joysticks[JOYSTICK_LY] = analogRead(JOYL_Y) - MID_LY;
		joysticks[JOYSTICK_RX] = analogRead(JOYR_X) - MID_RX;
		joysticks[JOYSTICK_RY] = analogRead(JOYR_Y) - MID_RY;
	}
}

void startup_banner()
{
	//Show Product name
	lcd.print(F("FTContr-"));
	lcd.setCursor(0, 1);
	lcd.print(F("oller"));
	delay(750);
	lcd.clear();
	//Show Version
	lcd.print(F("Version:"));
	lcd.setCursor(0, 1);
	lcd.print(F(VERSION));
	delay(750);
	lcd.clear();
	//Show Copyright
	lcd.print(F("(C)J.Bo-"));
	lcd.setCursor(0, 1);
	lcd.print(F("ehmer"));
	delay(750);
	lcd.clear();
}

void eeprom_save()
{
	//Save Mode
	EEPROM.update(EEPROM_MODE, mode);
	//Save display mode
	EEPROM.update(EEPROM_DISPLAY, display_mode);
	//Save emergency halt option
	EEPROM.update(EEPROM_HALT, config.emergency_halt);
	//Save Counter unit setting
	EEPROM.update(EEPROM_CUNIT, config.counter_unit);
	//Save Counter Debountce setting
	EEPROM.update(EEPROM_CDEB, config.counter_debounce);
	//Save Counter Multiplier
	EEPROM.update(EEPROM_CMULTI, config.counter_multi);
	//Save Counter Divider
	EEPROM.update(EEPROM_CDIVIDE, config.counter_divide);
}

void read_eeprom()
{
	uint8_t tmp = EEPROM.read(EEPROM_MODE);
	if (tmp > MODE_MAX_VAL) //IF we dont know the read mode, then set it to the default one
		mode = MODE_DEFAULT;
	else
		mode = tmp;

	//Display mode
	tmp = EEPROM.read(EEPROM_DISPLAY);
	if (tmp > DISPLAY_MAX_VAL) //IF we dont know the read mode, then set it to the default one
		display_mode = DISPLAY_DEFAULT;
	else
		display_mode = tmp;

	tmp = EEPROM.read(EEPROM_HALT);
	if (tmp > 1)
		config.emergency_halt = 0;
	else
		config.emergency_halt = tmp;

	tmp = EEPROM.read(EEPROM_CUNIT);
	if (tmp > 1)
		config.counter_unit = 0;
	else
		config.counter_unit = tmp;

	tmp = EEPROM.read(EEPROM_CDEB);
	if (tmp > 1)
		config.counter_debounce = 0;
	else
		config.counter_debounce = tmp;
	
	tmp = EEPROM.read(EEPROM_CMULTI);
	if (tmp == 0xFF)
		config.counter_multi = 0;
	else
		config.counter_multi = tmp;

	tmp = EEPROM.read(EEPROM_CDIVIDE);
	if (tmp == 0xFF)
		config.counter_divide = 0;
	else
		config.counter_divide = tmp;
}

inline void failsafe_check()
{
	if (config.emergency_halt  && display_mode != DISPLAY_COUNT)
	{
		if (bitRead(PIND, 7) == 0)	//When Count input low, then activate the failsafe mode
		{
			failsafe = FAILSAFE_HALT;
		}
	}

	if (failsafe != FAILSAFE_OFF)
	{
		stop_motors();

		uint8_t tmp = 0;
		
		lcd.home();

		switch (failsafe)
		{
		case FAILSAFE_HALT:
			lcd.print(F("Em.Halt "));
			break;
		default:
			lcd.print(F("FAILSAFE"));
			break;
		}

		lcd.setCursor(0, 1);
		lcd.print(F("PressBTN"));
		
	}
}


/***************************************************
* BUTTON HANDLERS
****************************************************/

void button_pressedCallback()
{
	static long lasttime = 0;
	
	if (failsafe == FAILSAFE_OFF)
	{
		if (menu != MENU_HIDDEN)	//Toggle menu visibility
		{
			menu = MENU_HIDDEN;
			eeprom_save();
		}
		else
		{
			menu = MENU_SHOW;
			stop_motors();
		}

		if (millis() - lasttime < DOUBLECLICK_TIME) //If button was double clicked, activate FREEZE mode
		{
			if (display_mode == DISPLAY_COUNT)
			{
				counter_reset();
				menu = MENU_HIDDEN;
			}
			else
			{
				if (freeze == 0)
					freeze = 1;
				else
					freeze = 0;
				menu = MENU_HIDDEN;		//Hide menu
			}
			
		}
	}
	else
	{
		//Only switch of failsafe mode, when joysticks are not giving an output val, or the freeze mode is activated (because then the joystick vals donte become updated)
		if (joysticks[JOYSTICK_LX] < THRESHOLD_P && joysticks[JOYSTICK_LX] > THRESHOLD_N
			&& joysticks[JOYSTICK_LY] < THRESHOLD_P && joysticks[JOYSTICK_LY] > THRESHOLD_N
			&& joysticks[JOYSTICK_RX] < THRESHOLD_P && joysticks[JOYSTICK_RX] > THRESHOLD_N
			&& joysticks[JOYSTICK_RY] < THRESHOLD_P && joysticks[JOYSTICK_RY] > THRESHOLD_N 
			|| freeze == 1)
		{
			failsafe = FAILSAFE_OFF;
		}
	}

	lasttime = millis();
}

void button_releasedCallback()
{
	
}

void button_pressedDurationCallback(unsigned long duration)
{

}

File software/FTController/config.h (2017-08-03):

#pragma once

#ifndef _CONFIG_H
#define _CONFIG_H

#if defined(ARDUINO) && ARDUINO >= 100
#include "arduino.h"
#else
#include "WProgram.h"
#endif

#define MOTOR_DELAY		40

#define VERSION			"0.1a"
#define VOLT_REF_CAL	1126400L

#define JOY_MID			512
#define MID_LX			JOY_MID
#define MID_LY			JOY_MID
#define MID_RX			JOY_MID
#define MID_RY			JOY_MID
#define TOLERANCE		50
#define TOLERANCE_P		TOLERANCE
#define TOLERANCE_N		-TOLERANCE
#define THRESHOLD		300			//When a joystick input should be treated as logic 1
#define THRESHOLD_P		THRESHOLD	//positive threshold
#define THRESHOLD_N		-THRESHOLD	//negative threshold
#define MAXIMUM			520
#define MAXIMUM_P		MAXIMUM
#define MAXIMUM_N		-MAXIMUM

#define VOLT_DIV1		965		
#define VOLT_DIV2		100
#define VOLT_OFFSET		150
#define REF_1V1			1100

#define C_REF_1V1		1380
#define SHUNT_R			340L			//Shunt resistance in mOhm
#define CURRENT_V_OFFSET	0

#define CURRENT_AVG_N	12

#define DOUBLECLICK_TIME	300

#define COUNTER_DEBOUNCE	15

#define DISPLAY_FIX				//Define this if you want to use the VOLT_MEASURE PIN for DISPLAY_E

#endif

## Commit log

2017-04-03 GITIGNORE und GITATTRIBUTES hinzufügen.
2017-04-03 Freeze the input value, when double click the menu button.
2017-07-29 Added a temperature view menu. Prepared some functions for counter.
2017-07-30 Failsafe message does not flicker any more.
    [FTController.ino]
2017-07-31 Added a counter function. Allow to switch between Hz and RPM display.
2017-07-31 Allow usage of both x and y axis on right stick for toggeling settings.
2017-07-31 Added counter mode, where the count get increment whenever a falling edge on input is present. Reset with double click.
    [FTController.ino, helpers.h]
2017-08-03 Added Current measurement.
2017-08-03 Use two digits for Voltage in display_power
2018-08-14 Added KiCAD files to project.
    [Drivers.sch, FTController.dsn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]
2018-08-15 Updated KiCAD files for KiCAD 5.0 and exported schematics
    [Drivers-2018-08-15-10-36-21.sch, FTController-2018-08-15-10-36-21.sch, FTController.sch]
2018-08-15 Updated gerber files
    [FTController-B.Cu.gbl, FTController-B.Mask.gbs, FTController-B.SilkS.gbo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]
2018-08-15 Added interactive BOM for PCB.
2018-08-15 Moved arduino sketch into a FTController folder, so it can be opened with the arduino IDE easily.

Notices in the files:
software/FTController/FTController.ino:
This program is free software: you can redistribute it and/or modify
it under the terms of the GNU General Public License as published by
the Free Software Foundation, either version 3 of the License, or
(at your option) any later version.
